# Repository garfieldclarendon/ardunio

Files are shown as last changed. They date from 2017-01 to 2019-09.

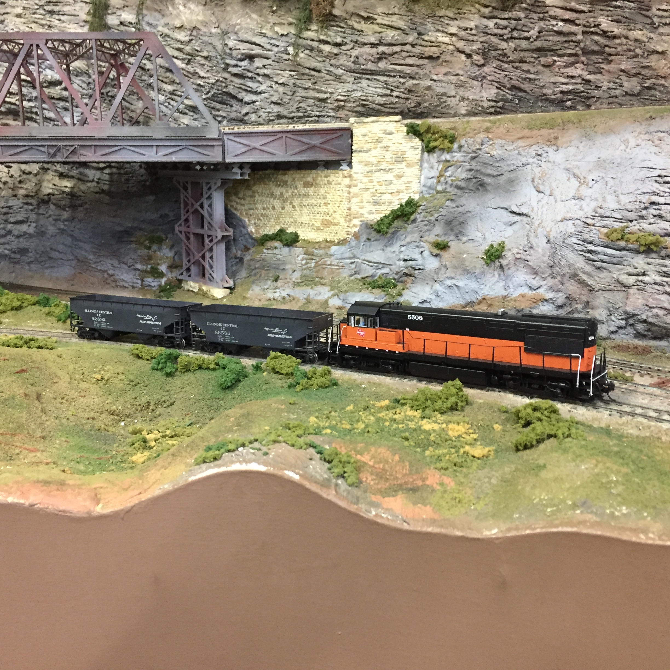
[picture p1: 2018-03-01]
Documents/Images/Train_enroute.JPG

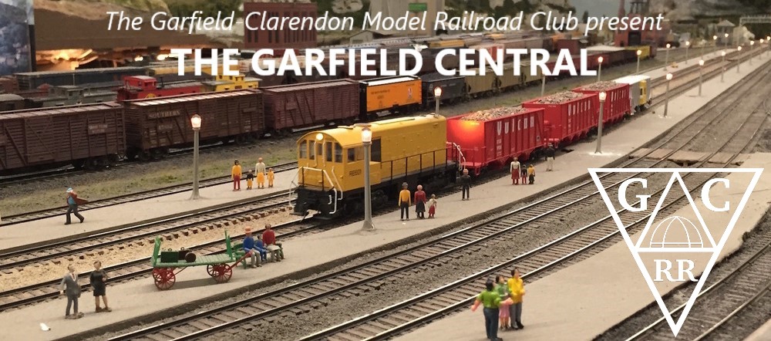
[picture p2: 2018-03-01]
Documents/Images/LayoutPic1.jpg

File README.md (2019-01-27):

# Layout Control System (LCS)

A project that uses ESP8266 WiFi modules that communicate with a Raspberry Pi server to control accessories on the Garfield-Clarendon Model Railroad Club.

### Prerequisites

The code running on the ESP8266 is developed using the Arduino IDE

The LCSServer application running on the Raspberry Pi makes use of the Qt framework.  The ESP8266 uses http calls to communicate with the LCSServer application  and UDP unicast messages to communicate with other ESP8266 controllers on the layout.  A separate RESTful API provides access to commands to activate routes, set turnouts and update data in the configuration database.

[Layout Control System Overview](https://github.com/garfieldclarendon/garfieldclarendon.github.io/blob/master/html/Documents/LCSOverview.pdf)

[Source Code Documentation](https://garfieldclarendon.github.io/html/index.html)

[API Documentation](https://garfieldclarendon.github.io/apidoc/index.html)

## Built With

* [Arduino](https://www.arduino.cc/en/Main/Software) - Arduino Tools
* [Qt](https://www.qt.io/) - Qt Framework
* [Eagle](https://www.autodesk.com/products/eagle/overview) - Eagle Printed Circuit Board (PCB) design software

## Contributing

Please read [CONTRIBUTING.md](https://gist.github.com/PurpleBooth/b24679402957c63ec426) for details on our code of conduct, and the process for submitting pull requests to us.

## Authors

* **John Reilly** - *Initial work*
* **Ryan Balla** - *Web Development*

## License

This project is licensed under the MIT License - see the [LICENSE](LICENSE) file for details

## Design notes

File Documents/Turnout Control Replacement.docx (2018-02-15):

# Turnout Control Replacement

# What You’ll Need

- Turnout motor cable
- Turnout Module (if needed. Each module controls two turnout motors)
- Communication Cable (for new module only)

# Installation

## Converting a turnout to LCS control involves 5 basic steps:

1. Enter the device and route entries into the LCS database.
2. Install the Turnout Module
3. Connect the turnout motor to the Turnout Module
4. Connect the Red and Green LED’s to the control panel(s) Output Module
5. Connect the panel button/switches to the control panel(s) Input Module

## Update the LCS software database:

1. Add the Turnout Device to the LCS System (Screen shot)
2. Identify which Turnout Module the new turnout device is going to be connected to. If this is a new module, add the module to the LCS System (Screen Shot)
a. Edit the new Turnout Device entry.
b. In the Assigned Controller Modules list, add a new entry - selecting the module identified in step 2 above. Enter the port number (0 or 1) to which the turnout will be wired. 0 is the bottom connection, 1 is the top. Each port is labeled on the circuit board.
3. In the search box, enter the name of the turnout created in step 1 above. Three entries should appear; the turnout device entry and two PanelOutput device entries which were automatically created with the turnout device. These entries will have the same name as the turnout with (Red) and (Green) appended to the end of the name.
a. Identify which Output Module the two LED’s are going to be wired to. Do this for each panel the turnout is displayed on.
b. Edit each PanelOutput device entry
c. In the Assigned Controller Modules list, add a new entry - selecting the module identified in 3.a. Enter the pin number the LED will be wired to. Starting at the bottom of the right output connector, the pins are numbered 0 – 7 then continue from the top of the left output connector numbered 8-15.
4. Add the route
a. Add the route entries
5. Add new PanelInput devices for each button/switch. NOTE: Add only one entry even if the button activates the turnout from more than one panel.
a. Identify the Input Module the button/switch will be connected to. Do this for each panel the turnout is controlled from.
b. Edit each PanelInput device entry
c. In the Assigned Controller Modules list, add a new entry - selecting the module identified in 5.a. Enter the pin number the button/switch will be wired to. Starting at the bottom of the right input connector, the pins are numbered 0 – 7 then continue from the top of the left input connector numbered 8-15.
6. Install the Turnout Module (if a new module is required). DO NOT CONNECT THE COMMUNICATION CABLE
7. Connect the turnout cable to the turnout motor and plug the cable into the assigned port.
8. Disconnect power from the controller
9. Verify the address dip-switch settings
10. Connect the communication cable
11. Connect power to the controller.
12. Verify the turnout is set to its normal position.
13. Verify the status of the turnout in the Admin application (screen shot)

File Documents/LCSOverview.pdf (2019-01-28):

## Garfield-Clarendon Model Railroad Club

# Layout Control System

### LCS Overview

The Layout Control System or LCS is a micro-controller based system used to control model railroad accessory devices such as turnout motors, signals, control panels, etc. The system is based around the ESP-12F ESP8266 (https://en.wikipedia.org/wiki/ESP8266) Wi-Fi module. This low cost, Wi-Fi-microcontroller module has the perfect combination of power and features which makes it ideally suited for a project of this type. For the purpose of this overview, the Layout Control System is referred to as “LCS” throughout this document.

4501 N Clarendon Avenue
Chicago, IL 60640

# Layout Control System

LCS Overview

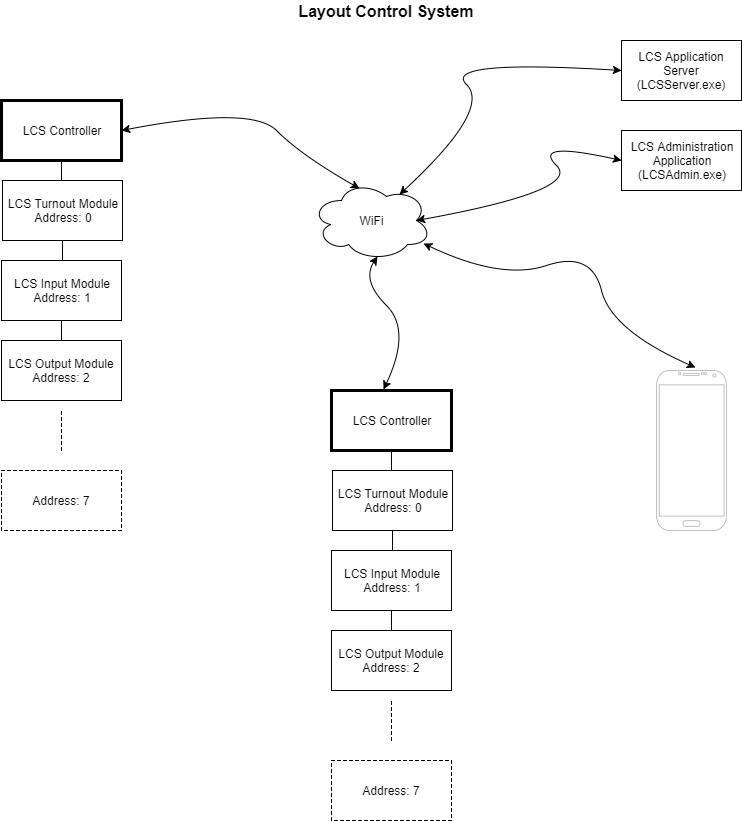
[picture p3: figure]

Figure 1 LCS Overview

# Layout Control System

LCS Overview

As pictured, LCS is broken down into the following components:

Controller | The ESP8266 based micro-controller board that controls the attached accessories. Each controller board can communicate with up to 8 module boards over the I2C (https://en.wikipedia.org/wiki/I%C2%B2C) serial bus.
Turnout Module | Controls two turnout motors and receives feedback from the turnout motor as to its current position (normal or thrown)
Input Module | 16 input pins are available to be used by control panel buttons and/or block detection units
Output Module | 16 output pins are available to be used by control panel LED’s and/or signals
Application Server | The application that manages the database which stores the configuration data that drives the system. The application server also acts as the interface between outside systems such as the NCE Command Station, smart phones, dispatcher panels, etc.
Administration Application | A user-friendly application for managing the system configuration data.

Table 1 LCS Components

### LCS Controller

The controller provides processing and communication. There are three types of controllers:

Class | Controller Type | Description
7 | Multi-Controller | The most common controller type. This controller manages multiple module boards connected via an I2C (https://en.wikipedia.org/wiki/I%C2%B2C) serial bus cable.
1 | Turnout Controller | A controller and turnout module combined into one board which can control two turnouts.
5 | Semaphore Controller | Semaphore Signal Controller which is a controller and turnout module combined into one board. The turnout module is used to run the motor that moves the signal arm.

Table 2 Controller Types

Most of the controllers on the layout will be the Multi-Controller as it can handle many more devices. Since we have only one Semaphore signal on the layout, there’s only one Semaphore Controller. Although there are three controller types,

# Layout Control System

LCS Overview

there are only 2 actual controller printed circuit boards. The Semaphore Controller uses the same board as the Turnout Controller. Internally, the three controllers use the same firmware. The firmware code knows what controller it’s actually running on based on the Controller Class setting in the controller’s configuration file (described shortly).

### LCS Modules

The LCS Controller does not directly control devices. Rather, each controller may have up to 8 module boards connected which, in turn, control the attached devices. There are 4 types of module boards (see Table 5). Module boards are connected using a communication cable (figure 2).

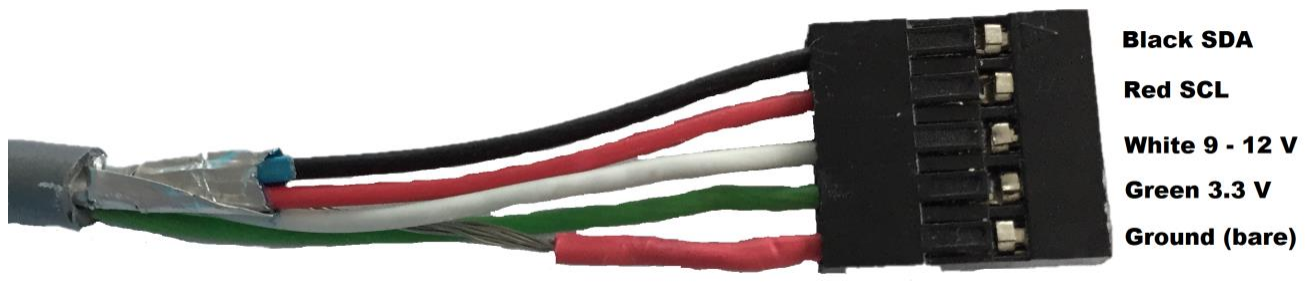
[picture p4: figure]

Figure 2 Communication Cable

The black and red (SDA, SCL) wires are the actual communication wires used by the I2C (https://en.wikipedia.org/wiki/I%C2%B2C) bus. The white wire acts as a pass-through power source which can be used by modules to power devices that require higher voltages (like turnout motors). Although labeled as 9 – 12 V, the voltage is actually the same as the power supply plugged into the controller board. If the power supply is a 9 volt power supply, then the voltage between the white wire and the ground (red) wire will be 9 volts. The green wire is the 3.3 V output of the voltage regulator on the controller board. The regulator will adjust the input voltage to keep it as close to 3.3 volts as possible. This supplies the regulated voltage needed by the IC chips on the module boards.

Each module has a corresponding entry in the database which defines the module’s type, which controller it’s connected to and the module’s address. Module boards must have a unique address of 0 to 7. To achieve this, a three-position dip switch is used to set the module’s address:

# Layout Control System

LCS Overview

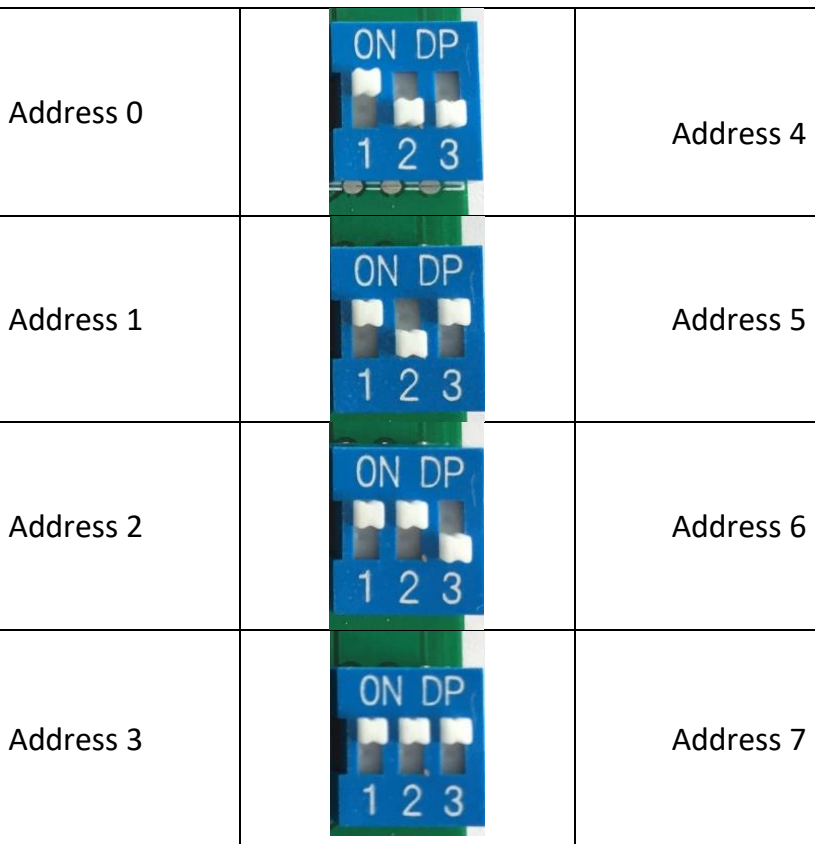
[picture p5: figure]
Address 0; Address 4; Address 1; Address 5; Address 2; Address 6; Address 3; Address 7
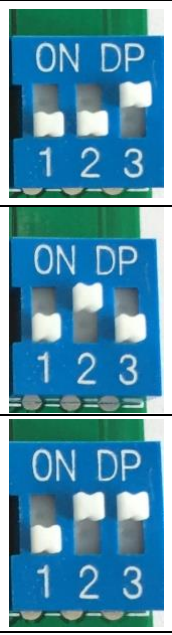
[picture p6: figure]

Table 3 Address DIP switch settings

NOTE: The address set with the dip switches must match the address entered in the module’s entry in the database. Module boards may be connected to the controller in any order.

### LCS Device

LCS treats everything it interacts with as a device. A device represents an item on the layout that the system either controls or monitors. LCS supports the following types of devices:

# Layout Control System

LCS Overview

Turnout | A slow-motion motor Which controls a turnout on the layout.
Panel Input | A momentary push-button or switch on a layout control panel. These buttons, when pressed, activate a route which aligns one or more turnouts to a desired route
Panel Output | A panel LED indicator light. The LED indicates the current state of a turnout , route or block occupancy.
Signal | A three-light (LED) signal head.
Block Occupancy Detector | Monitors an external block detection circuit.

Table 4 Device Types

Like modules, each device has a corresponding database entry which defines the device type, assigned module and the port (pin) on the module the device is connected to.

### LCS Configuration Files

JSON (https://en.wikipedia.org/wiki/JSON) formatted configuration files are stored in the controller’s permanent flash memory. When the controller starts up, the first file it loads is the controller’s configuration file:

{
"controllerClass": "7",
"controllerID": "34",
"controllersToNotify": [{
"controllerID": "28"
}
],
"modules": [{
"address": "0",
"class": "8"
}, {
"address": "1",
"class": "9"
}, {
"address": "2",
"class": "9"
}
]
}

This is the configuration file for the CA Auxiliary control panel. Here’s what the entries mean:

“controllerClass” contains a number that represents the type of controller board (see table 2)

# Layout Control System

LCS Overview

“controllerID” contains the unique ID of the controller from the controller table in the database. Each controller is identified by a controllerID and a serialNumber. The controllerID entry is used to cross-reference the controller with the modules connected to it. The serial number is a unique id assigned by the manufacturer to each ESP8266 Wi-Fi module. The reason for the two identifiers is so that if a controller needs to be replaced, the only field that needs to be updated in the database is the serial number field.

“controllersToNotify” is a list of controller ID’s that need to be notified whenever the state of a connected device changes. Since this configuration is from the CA Auxiliary panel, the device that will trigger a notification message is a Panel Input device (panel button). When the user presses a button on the panel, the Panel Input Device will generate a message which will be sent to each controller listed in this section. In this example just one controller will be notified which is controller 28 – “CA West End Multi 1” controller.

“modules” is a list of modules connected to this controller via the I2C (https://en.wikipedia.org/wiki/I%C2%B2C) serial bus . Each module entry contains the address of the module and the module class:

Class | Module Type | Software Module Class
1 | Turnout Module | TurnoutModule
5 | Semaphore Module | TurnoutModule
8 | Input Module | InputModule
9 | Output Module | OutputModule
Table 5 Module Types

In this example, three modules are connected; an input module (class 8) and two output modules (class 9) with the addresses of 0, 1 and 2 respectively.

Next, the LCS Controller creates software modules that manage the interaction between the physical module board and the devices connected to the module. The LCS Controller communicates with each module via the I2C serial bus communication cable (Figure 2).

Each module’s configuration file is the next file to be loaded:

# Layout Control System

LCS Overview

{
"devices": [{
"c": "2",
"id": "44",
"p": "0"
}, {
"c": "2",
"id": "43",
"p": "1"

}, {
"c": "2",
"id": "52",
"p": "15"
}
],
}
Each JSON file contains a list of devices attached to the controller module. In this example, the devices are all the same; device class 2 – Panel Input, as defined by the “c”: “2” entry. Each device entry in this example file represents a button on the CA Auxiliary Panel. The other two properties in the device configuration represent the device ID “id” and the pin assignment “p”. Putting it all together, the first entry is a Panel Input device (2) with a device ID of 44 (id) and is assigned to pin 0 (p). For each entry in the file, a software class that manages the device is created. This software class has all the logic needed to manage the device. Once an instance of the device class is created, the next step is to load the configuration data for that device. As you probably guessed, this involves loading a JSON file for each device attached to the controller module:

{
"ROUTEID": "19",
"deviceClass": "2"
}

Continuing with the previous example, this is the configuration for the first device entry, device 44. The important line in this file is the ROUTEID entry. This represents the route that gets activated when the button connected to pin 0 is pressed on the CA Auxiliary Panel.

The reality is, the configuration files are not actually stored as JSON files. The reason is these files must be loaded and then parsed by the micro-controller and converted to a binary structure it can actually use. This process is pretty slow, so instead, the binary structure is what is actually stored in the file. The JSON format is only used when the controller needs to download the configuration files from the

# Layout Control System

LCS Overview

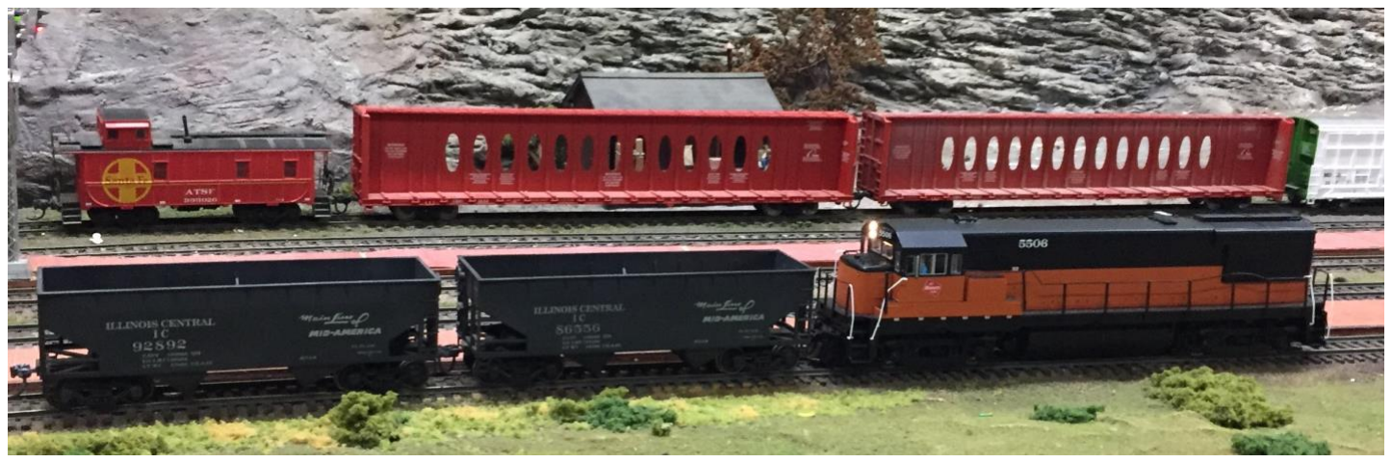
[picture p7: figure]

server. Once downloaded, the JSON information is parsed and converted to the binary structure and saved to a file.

### LCS in Action

The best way to understand how a system works is by following an example. Let’s do a simple run to the Gaskill Mine.

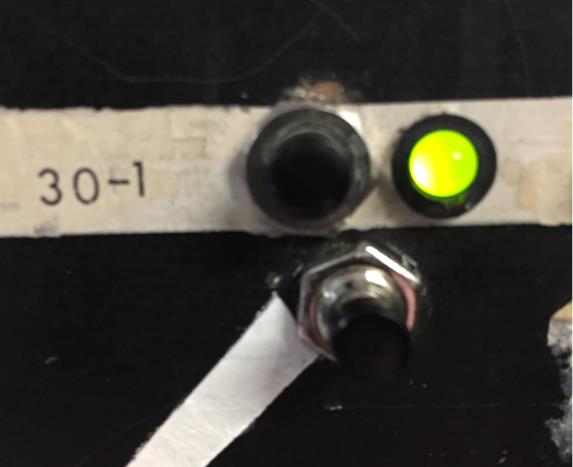
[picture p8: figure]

Milwaukee Road 5506 has two empties to drop off at the Gaskill Mine and awaits the turnout alignment to proceed into the mine branch. Currently, the mine’s turnout, T30-2, is aligned for the main, its normal route, as indicated by the green LED indicator on the CA panel.

In order to route the train to the mine branch, we need to press the bottom button. But what is really happening when the button is pressed?

# Layout Control System

LCS Overview

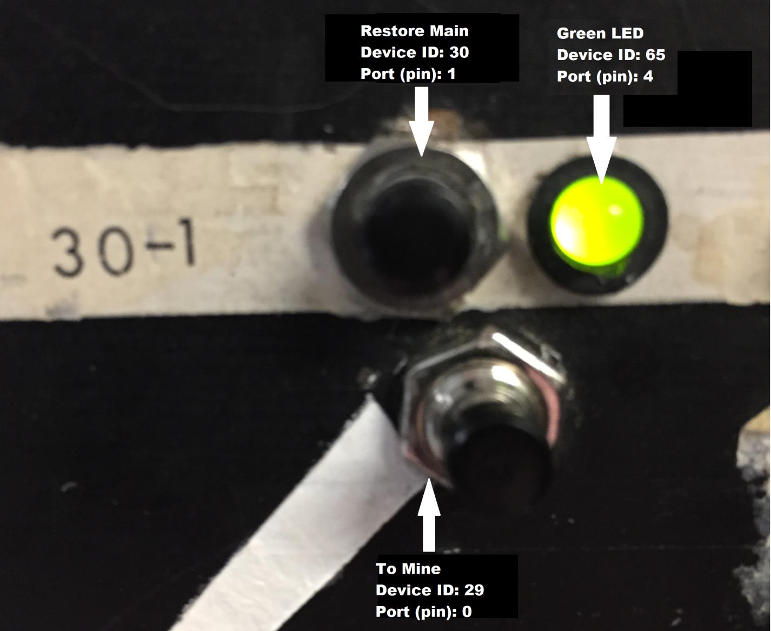
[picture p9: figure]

LCS treats each item it interacts with as a device. In the picture above, we have three devices listed; two buttons and one LED. The reality is, as we’ll see in a moment, there are really 4 devices as the LED is really two LEDs in one package; a red and a green. Notice that each device has a name, a unique ID and a port/pin assignment. In addition each device is assigned to a module that actually controls the device. In this example there are two modules; an Input Module and an Output Module. Let’s look at the database entries that make up this example:

# Layout Control System

LCS Overview

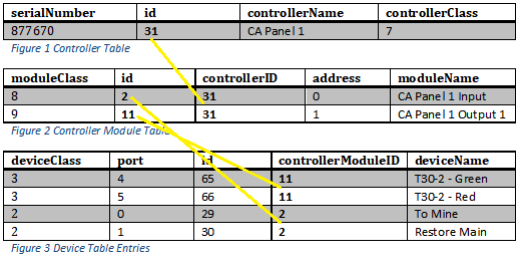
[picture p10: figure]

Note the additional entry in the device table (figure 3) for the “T30-2 – Red” LED device. Also note how the entries in each table are crossed reference with the table above it: The controller entry of id 31 is cross referenced in each entry in the module table via the controllerID field. Each device is cross referenced with its assigned module via the controllerModuleID field. Using this information, the controller has almost everything it needs to manage the buttons and LEDs. It knows how to interact with each device but not when each device LED should be on or off. For that information, we need to dig a little deeper into each device entry.

Devices have properties that are unique to each device type. These properties are stored in another database table called “deviceProperty”. Let’s look at the first button we’re going to press, the “To Mine” button, and examine its device property entry:

id | deviceID | key | value
7 | 29 | ROUTEID | 7
Figure 3 Device Property Table

This type of table is referred to in programming terms as a “key/value pair” table. In this case, “ROUTEID” is the key and “7” is the value. This data is used by the PanelInputDevice class to know what route to activate when a button is pressed; in this case, route 7.

As you probably guessed by now, each route is stored in its own database table called “route” and has a corresponding table, “routeEntry”, which contains an entry

# Layout Control System

LCS Overview

for each turnout the route needs to set when the route is activated. Let’s take a look at route 7:

id | routeName | routeDescription
7 | CA 1 | To Mine
Figure 4 Route Table
id | routeID | deviceID | turnoutState
11 | 7 | 7 | 3
Figure 5 Route Entry Table

Route 7 has one Route Entry item; Turnout device ID 7 (T30-2). When route 7 is activated, the Turnout Device will set the turnout with ID 7 to the turnout state of 3 (Diverging).

Let’s put it all together. When we push the bottom button, the InputModule will detect that the pin that button is connected to, pin 0, has changed. This information is passed on to the PanelInputDevice which activates route 7. How is route 7 actually activated? By sending a message!

UDPMessage and the Wi-Fi Network

The way one controller talks to another controller and the Application Server is via the Wi-Fi network. Because the ESP8266 is a very basic micro-controller with limited speed and memory, we need an efficient, low-overhead solution for sending messages between devices. The User Datagram Protocol, UDP, (https://en.wikipedia.org/wiki/User_Datagram_Protocol) is the ideal solution for this problem. UDP is very fast and efficient. The tradeoff is reliability. UDP by itself is an unreliable protocol, meaning there is no guarantee the message will actually reach its intended destination. The LCS Controller compensates for this by retrying each message until it reaches its target controller.

In our example, the PanelInputDevice creates a UDPMessage (https://garfieldclarendon.github.io/html/class_u_d_p_message.html) containing the route ID of 7 which is sent to the controllers in the Notification List from the controller 31’s configuration file. In this file is the controllersToNotify section:

"controllersToNotify": [ { "controllerID": "28" } ]
In this case, the message is sent to controller “28 - CA West End Multi 1” which is the controller that the T30-2 turnout is connected to.

# Layout Control System

LCS Overview

On the receiving end, controller 28 forwards the message to the TurnoutDevice that is managing T30-2. Let’s take a look at its configuration file:

{
"deviceClass": "1",
"routes": [{
"routeID": "7",
"turnoutState": "3"
}, {
"routeID": "8",
"turnoutState": "1"
}
]
}
As you can see, each turnout stores the routes its’ assigned to and the state they need to be set to when the route is activated. In our example, when the message arrives, TurnoutDevice T30-2 will lookup route 7 and set its state to “3 – Diverging”. It then immediately sends out a new message indicating the turnout is now changing by setting its current state to “2 – To Diverging” indicating the turnout is in the process of throwing to the diverging route. The TurnoutDevice’s status message is sent to controller 28’s notification list:

"controllersToNotify": [{
"controllerID": "31"
}, {
"controllerID": "34"
}, {
"controllerID": "35"
}, {
"controllerID": "30"
}
]
Notice there are many more controllers that need to be notified when something connected to controller 28 changes! The first controller in the list is our example controller,”31 - CA Panel 1”. It also sends messages to:
- 34 - CA Aux Panel
- 35 - Overhead Panel
- 30 - Semaphore1
Controller 31 forwards this message to the PanelOutputDevices that manage device ID “65 – T30-2 Green” and device ID “66 – T30-2 Red”. The device properties for device 65 are:

# Layout Control System

LCS Overview

id | deviceID | key | value
89 | 65 | ITEMID | 7
90 | 65 | ONVALUE | 1
91 | 65 | FLASHINGVALUE | 4

ITEMID is set to the device the PanelOutputDevice is monitoring; in this case device ID “7 – T30-2” and sets its output pin ON when T30-2 is “1 – Normal” and flashing when T30-2 is “4 – To Normal”. In our example, the current state of T30-2 is “2 – To Diverging”. Since this doesn’t match either of the two entries, the PanelOutputDevice sets the output to LOW turning the green LED off.

Device 66 has the following entries:

id | deviceID | key | value
89 | 66 | ITEMID | 7
90 | 66 | ONVALUE | 3
91 | 66 | FLASHINGVALUE | 2

Which means T30-2’s current state of “2 – To Diverging” matches its FLASHINGVALUE entry, so the PanelOutputDevice sets the output to a blinking state; turning the red LED ON and then OFF every ¾ of a second.

The result is T30-2 goes from its normal route:

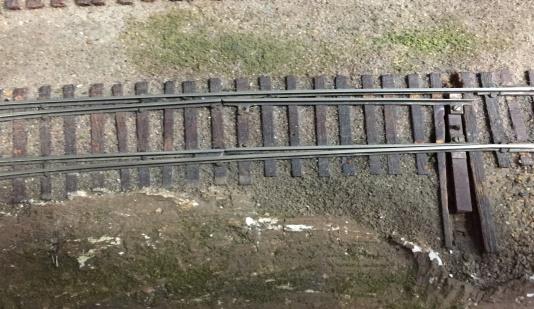
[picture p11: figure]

To its diverging route:

# Layout Control System

LCS Overview

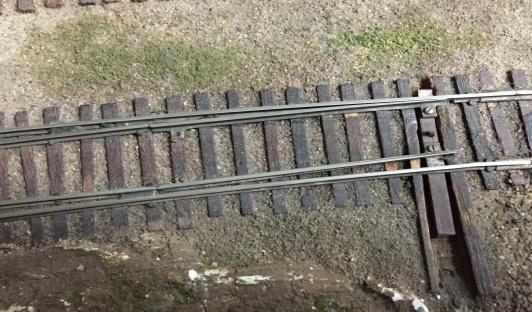
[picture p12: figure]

Now that the turnout is fully thrown, the TurnoutDevice sends a final status message, this time with the status of “3 – Diverging” as T30-2’s current state. The new state of 3 matches the PanelOutputDevice 66’s ONVALUE configuration entry so it sets the output to ON turning on the red LED (the LED stops flashing).

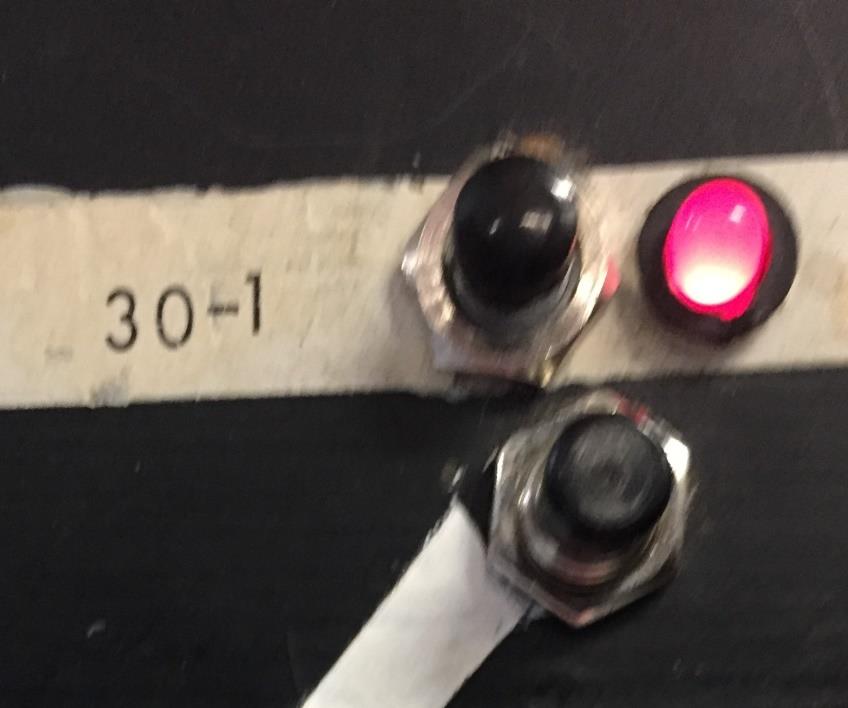
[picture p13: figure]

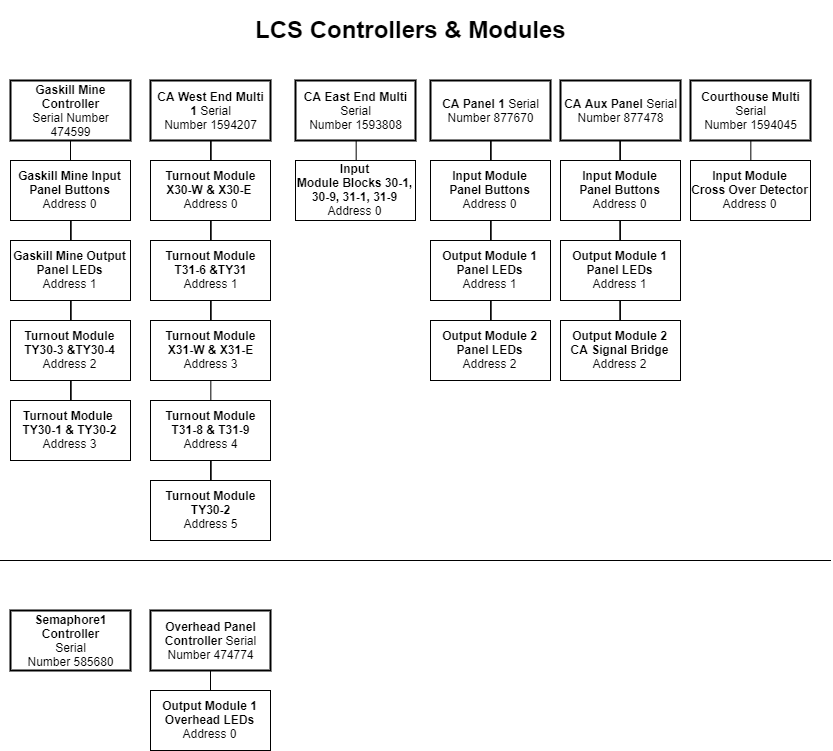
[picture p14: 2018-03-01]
Documents/Images/Overview1.png

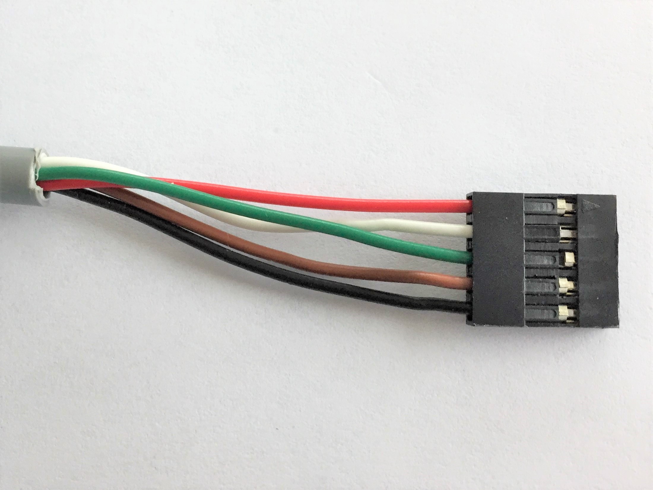
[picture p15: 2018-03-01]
Documents/Images/Turnout_Module_Cable.JPG

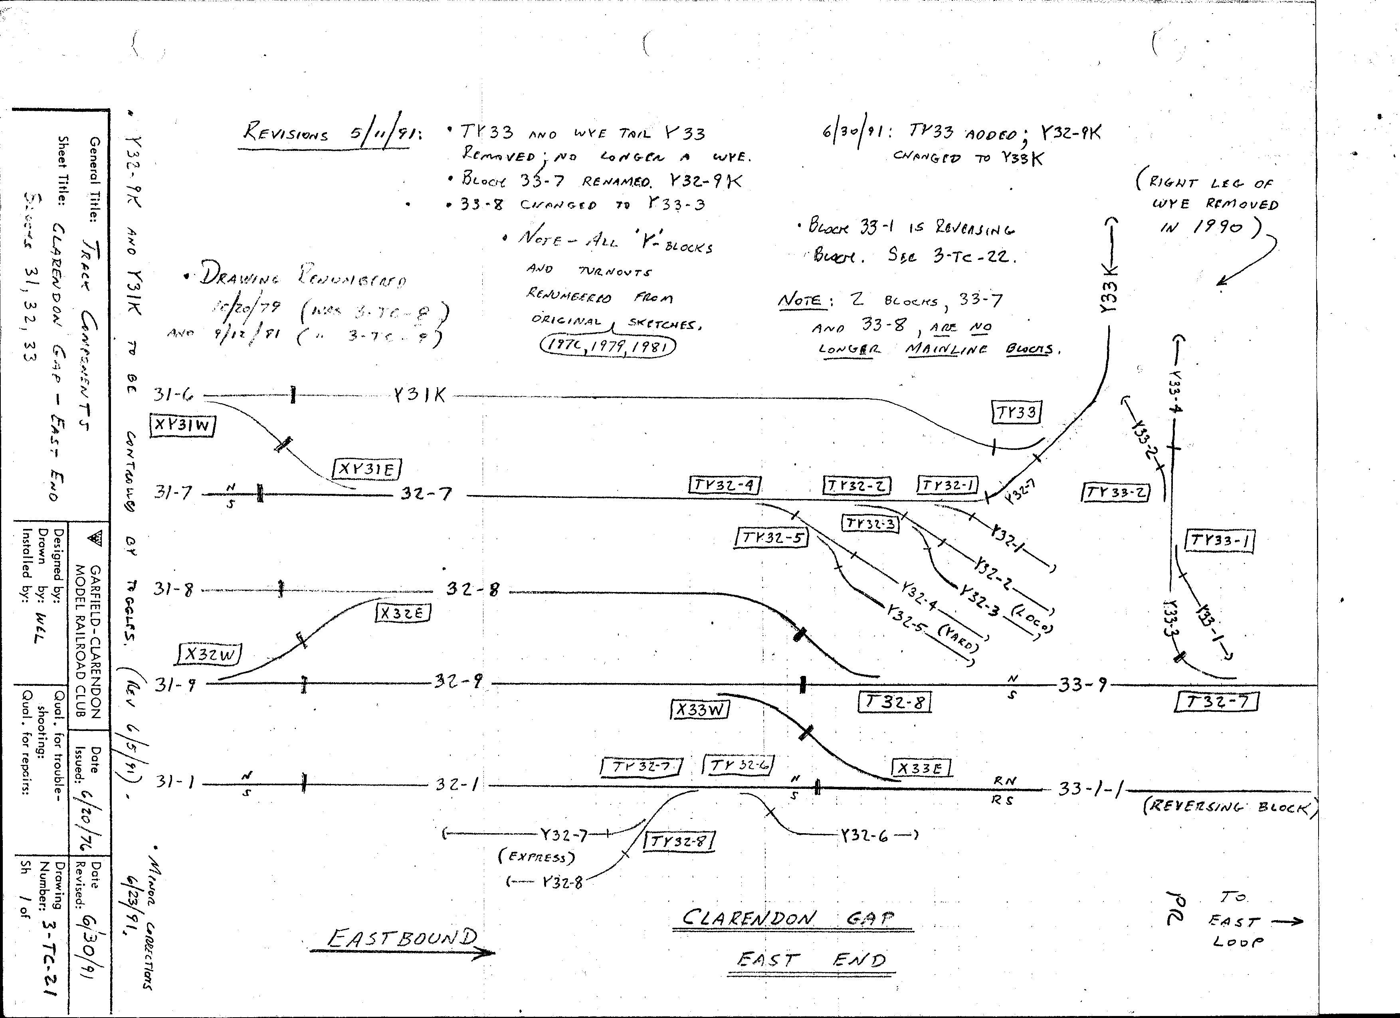
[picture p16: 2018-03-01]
Documents/Images/CA_EastEnd.png

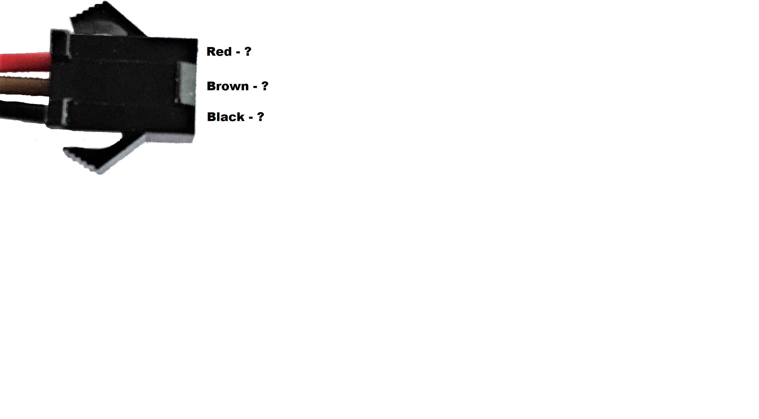
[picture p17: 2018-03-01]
Documents/Images/Turnout_Frog_Cable.png

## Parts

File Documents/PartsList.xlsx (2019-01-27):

MASTER PARTS LIST
ITEM | QUANTITY | COST | PER | STOCK
Resistors - 10k Ohm | 100 | $4.04 | $0.04 | 110
Resistors - 3.3k Ohm | 100 | $6.16 | $0.06 | 119
Resistors - 220 Ohm | 100 | $6.43 | $0.06 | 160+
DIP Switch - 3 position | 20 | $13.64 | $0.68 | 3
Connector - 1x8 Dupont | 10 | $3.30 | $0.33
Connector - 1x5 Dupont | 10 | $3.84 | $0.38
DC Power Jack Socket | 22 | $5.62 | $0.26 | 13
L293D Stepper Motor Driver | 10 | $8.99 | $0.90 | 14
ESP-12F ESP8266 Wifi Controller | 10 | $26.00 | $2.60 | 15
LD1117V33 Voltage Regulator 3.3v | 12 | $7.99 | $0.67 | 6
MCP23017-E I2C Expander (16 pin) | 25 | $26.25 | $1.05 | 8
MCP23008-E I2C Expander (8 pin) | 10 | $10.80 | $1.08 | 13
Single Row 40Pin Male Header | 100 | $8.99 | $0.09
Capacitor 10 uF | 1000 | $13.99 | $0.01 | 900+
Capacitor 1 uF | 100 | $5.63 | $0.06 | 60
LED Red | 100 | $6.57 | $0.07 | 13
Printed Circuit Board | 40 | $43.00 | $1.07
LCS CONTROLLER
Capacitor 10 uF | 1 | $0.01 | $0.01
Capacitor 1 uF | 1 | $0.06 | $0.06
5 Pin Male Header | 9 | $0.01 | $0.10
DC Power Jack Socket | 1 | $0.26 | $0.26
Resistors - 220 Ohm | 2 | $0.06 | $0.13
Resistors - 3.3k Ohm | 2 | $0.06 | $0.12
ESP-12F ESP8266 Wifi Controller | 1 | $2.60 | $2.60
LD1117V33 Voltage Regulator 3.3v | 1 | $0.67 | $0.67
LED Red | 1 | $0.07 | $0.07
Printed Circuit Board | 1 | $1.07 | $1.07
 |  |  | ------------
TOTAL |  |  | $5.09
LCS INPUT MODULE
Capacitor 10 uF | 1 | $0.01 | $0.01
5 Pin Male Header | 2 | $0.01 | $0.02
8 Pin Male Header | 2 | $0.02 | $0.04
MCP23017-E I2C Expander (16 pin) | 1 | $1.05 | $1.05
Resistors - 10k Ohm | 3 | $0.04 | $0.12
Resistors - 3.3k Ohm | 16 | $0.06 | $0.99
DIP Switch - 3 position | 1 | $0.68 | $0.68
Printed Circuit Board | 1 | $1.07 | $1.07
 |  |  | ------------
TOTAL |  |  | $3.99
LCS OUTPUT MODULE
Capacitor 10 uF | 1 | $0.01 | $0.01
5 Pin Male Header | 2 | $0.01 | $0.02
8 Pin Male Header | 2 | $0.02 | $0.04
MCP23017-E I2C Expander (16 pin) | 1 | $1.05 | $1.05
Resistors - 10k Ohm | 3 | $0.04 | $0.12
Resistors - 220 Ohm | 16 | $0.06 | $1.03
Printed Circuit Board | 1 | $1.07 | $1.07
DIP Switch - 3 position | 1 | $0.68 | $0.68
 |  |  | ------------
TOTAL |  |  | $4.03
LCS TURNOUT MODULE
Capacitor 10 uF | 1 | $0.01 | $0.01
5 Pin Male Header | 4 | $0.13 | $0.53
L293D Stepper Motor Driver | 1 | $0.90 | $0.90
Resistors - 10k Ohm | 3 | $0.04 | $0.12
Resistors - 3.3k Ohm | 4 | $0.06 | $0.25
MCP23008-E I2C Expander (8 pin) | 1 | $1.08 | $1.08
DIP Switch - 3 position | 1 | $0.68 | $0.68
Printed Circuit Board | 1 | $1.07 | $1.07
 |  |  | ------------
TOTAL |  |  | $4.64

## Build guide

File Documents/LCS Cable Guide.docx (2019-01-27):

LCS Cable Guide

Communication Cable

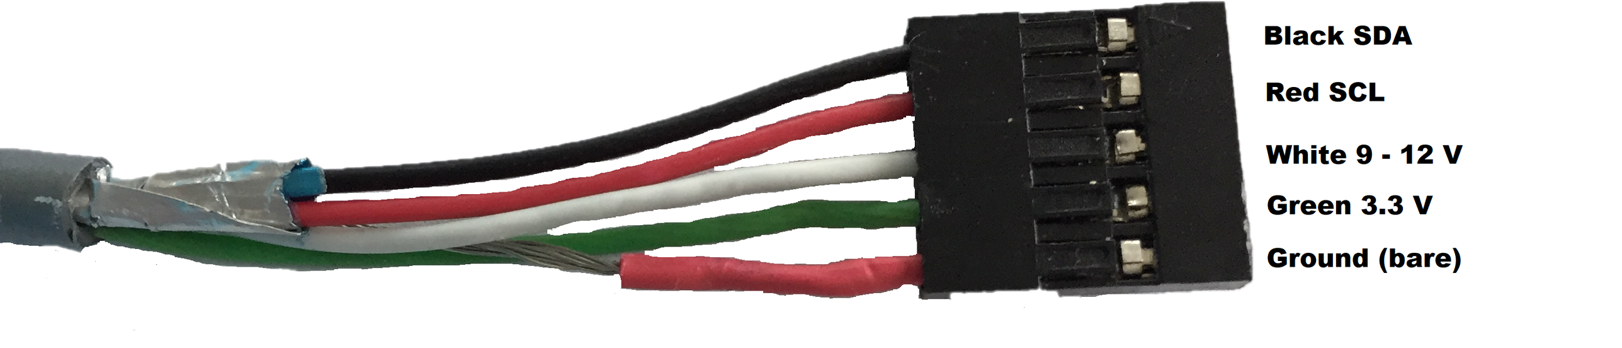
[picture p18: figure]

This cable is used to connect the controller board to module boards. The cable can also be connected between two module boards.

Turnout Motor Cable

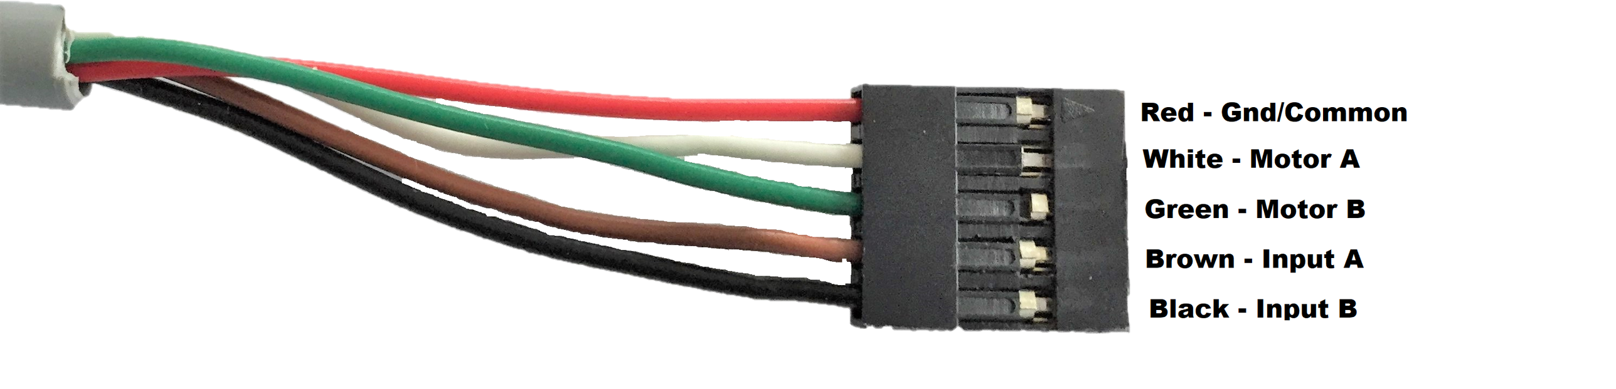
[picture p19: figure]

This cable connects a Turnout Module board to a turnout motor.

Note:

White: Motor +

Green: Motor –

Brown: Signal-Main

Black: Signal Diverging

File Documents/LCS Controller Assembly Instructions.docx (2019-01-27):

Garfield-Clarendon Model Railroad Club

Layout Control System

4501 N Clarendon Avenue

Chicago, IL 60640

LCS Controller Assembly Instructions

# What you’ll need

To assemble a LCS Controller, have the following tools at your side.

1. LCS Controller printed circuit board
2. Soldering iron
3. Solder (Rosin Core)
4. Wire cutters
5. Small screw driver
6. LCS Parts kit

# Getting Started

Plug in your soldering iron and place the LCS Controller circuit board in front of you as pictured

 [picture of blank board]

# Begin Assembly

To make assembly as simple as possible, start by placing the flattest items first followed by taller items in order of height.

1. Begin by soldering the 4 resistors in place. Resistors are labeled as 220 ohm (2) and 3.3 k ohm (2) on the printed circuit board. The orientation of the resistor is not important. [picture with resistors]
2. Place the voltage regulator in place as pictured. [picture with regulator]
3. Bend the voltage regulator backwards until the hole in the regulator’s heat sink aligns with the hole in the circuit board. The hole alignment does not have to be exact. [picture with regulator in place]
4. Solder the voltage regulator in place.
5. Place the pin headers onto the ESP 8266 module. The pin headers can be broken at any pin to create a header with the correct number of pins. Start by lining up the first pin of the header with the first hole in the ESP 8266. With your fingers, mark the last pin. Break the pin header at this point. Do this for both sides of the ESP 8266 module. The pins fit very tightly into the module so it takes a bit of force to properly insert the pins into the unit. It’s easier to place the unit on a flat surface with the pins facing down and firmly press on the center of the ESP9 8266 module until the pins slide into place. Adjusting pressure side-to-side may be necessary to get the pins properly seeded.
6. Very carefully, solder each pin to the ESP 8266. This is, by far, the most challenging soldering job. Be very careful not to let the solder cross over to the adjacent pins or the metal cover.
7. Place the ESP 8266 on the circuit board as pictured and solder into place. [picture with esp8266]
8. Solder the 8 5-pin headers and the 1 4-pin header in place. Like the header for the ESP 8266, these headers are also break-away. [picture with annotations]
9. Solder the 10uf capacitor in place. Align the capacitor with the negative lead (short lead marked with a silver line with a – sign) with the hole marked with a “-“. [picture with 10uf capacitor in place]
10. Solder the .1uf capacitor in place. Align the capacitor with the negative lead (short lead marked with a silver line with a – sign) with the hole marked with a “-“. [picture with .1uf capacitor in place]
11. Solder the red LED in place with the flat side/shorter lead aligned with the bottom hole.
12. Solder the power jack in place as pictured. Use a generous amount of solder on each of the three connections; making sure the solder completely covers the hole.

# Upload Firmware

The unit is now ready to be programmed! To upload the firmware, the LCS Controller needs to be connected to the club’s computer located in the overlook.

1. Plug the programming serial cable into a USB port on the computer and set the switch on the box to “upload”. [picture of the serial cable and box]
2. Connect the other end of the serial cable to the 5-pin header to the left of the ESP 8266 module on the printed circuit board with the blue wire side of the connector aligned with the bottom pin of the header as pictured [cable attached to board with annotation of blue wire]
3. Connect the power supply (from the LCS parts kit) to the LCS Controller. The red LED should light on the controller.
4. Launch the Arduino IDE program by double-clicking the icon on the computer’s desktop [screenshot of desktop]
5. Load the LCSController project. Go to File->Open and browse to the Document->Arduino->LCSController directory. Select the LCSController.ino file:

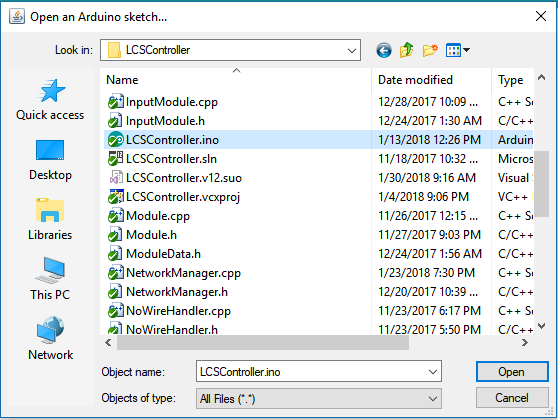
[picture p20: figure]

6. Double check the settings by selecting the Tools menu item. Verify the settings look like this:

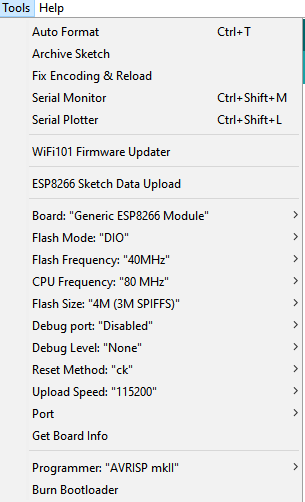
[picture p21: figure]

The important settings are:

- Board: “Generic ESP8266 Module”
- Flash Mode: “DIO”
- Flash Frequency: “40MHz”
- CPU Frequency: “80 MHz”
- Flash Size: “4M (3M SPIFFS)”
- Upload Speed: “115200”
7. Upload the firmware by selecting Sketch->Upload. The Arduino IDE program will compile the LCS Controller firmware and then begin the process of uploading the firmware to the controller. You’ll know the process is working when you see the blue LED on the LCS Controller flashing.
8. After the blue LED stops flashing and the Arduino program indicates the firmware uploaded successfully, unplug the controller.
9. Set the switch on the USB serial cable box to “serial”.???????
10. From the Arduino IDE program, select Tools->Serial Monitor
11. Change the baud rate to 38400 using the drop-down box in the lower right corner. The serial monitor window should look like this: [screen shot of serial monitor]
12. Plug in the LCS Controller.
13. Make note of the serial number printed out in the serial monitor. The LCS Controller will “boot-up” and print out some information about the firmware version number and the controller’s serial number (among other things). Write the serial number on a piece of masking tape and place it on the bottom of the LCS Controller board.
14. Un-plug the unit.

Layout Control System LCS Controller Assembly Instructions

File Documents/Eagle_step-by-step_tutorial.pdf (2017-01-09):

# EAGLE Tutorial

## Introduction

Eagle is a PCB CAD program for designing and laying out printed circuit board (PCB) designs. A freeware version is available as a download, which is what we will use in this Step-by-step tutorial.

http://www.cadsoftusa.com/download-eagle/

EAGLE works in two stages: Schematic capture and PCB design. In the first, the circuit connectivity is designed using the standard component symbols with which we are all familiar. In the second stage, the components are positioned on the printed circuit board and then traces between connected components are laid out. EAGLE makes this easier by preserving the connections between components and also applying various electrical and design rule checks in order to make sure the board will function as expected!

In this tutorial we are going to begin by designing a PCB board for the active low pass filter below, and then in groups of two you will design a PCB for the potentiostat circuit provided in this document. The
low pass filter will have the following component values, and will run off of a | supply.
This gives an approximate cut-off frequency | of 7.95 Hz and a passband gain of -10.

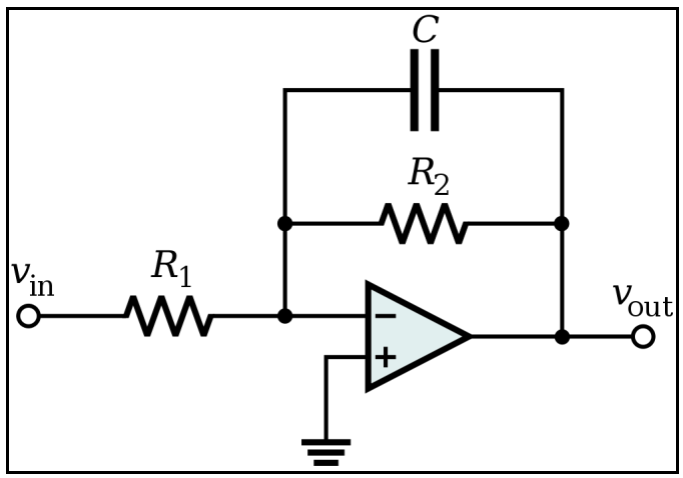
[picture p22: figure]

Figure 1: Active Low Pass Filter Circuit (http://en.wikipedia.org/wiki/Low_pass_filter)

## Part 1: Low Pass Filter

### Getting Started

1. Start Cadsoft EAGLE from the windows start menu (Start → Programs → EAGLE Layout Editor 5.x.x → EAGLE 5.x.x)
2. The first time that you run EAGLE, it will ask whether you would like to create a directory, click yes.
3. Expand the ‘Projects’ node of the tree on the left of the EAGLE menu.
4. Right click on the ‘eagle’ folder and select ‘New Project’. Name it ‘LPF’ (for low pass filter).
5. Right click on the LPF project folder (coloured in red) and select New → Schematic.

### Creating the Schematic

1. Select File → Save and save the schematic as ‘LPF Schematic.sch’.
2. First of all, add all of the parts we will need, in this case that is two resistors, a capacitor, and an opamp. We are going to use 0603 sized resistors and capacitors, and a through-hold DIP (Dual Inline Package) opamp.
a. Click on the ‘Add’ icon on the left-side toolbox – .
b. Start by adding the opamp, type ‘*LM*741*’ into the search box and press Enter.
c. Select the ‘DIL08’ version of the component and click ‘OK’. Click on the schematic to place the part. Press the right mouse button twice to rotate the part and then click the center mouse button once to mirror the part. This will orient the positive and negative terminals of the gate properly.
d. Press ESC to return to the ADD dialog.
e. In the ADD dialog, change the search term to be blank and press Enter.
f. Scroll down until ‘rcl’ appears in the list of parts. Expand ‘rcl’ and then expand the ‘R-US_’. Scroll down to ‘R-US_R0603’, select it, and
press ‘OK’. Place to resistors
g. Press ESC again to return to the ADD dialog.
h. Go back up to the root of the ‘rcl’ library and expand the ‘C-EU’ node.
i. Find the ‘C-EUC0603’ part and press OK. Place the part as per the schematic.
j. Press ESC and then ESC again to exit ADD mode.
3. At this point the schematic should look like Figure 2.
4. Now for the connectivity! Select the ‘NET’ tool from the

toolbox – .

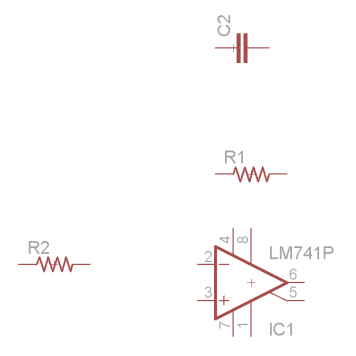
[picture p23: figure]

Figure 2: Basic part pl acement.

5. Draw wires between all of the relevant terminals as per the original schematic. Note: Double click to terminate the current NET. Select the ‘Junction’ tool ( ) and click to place junctions between wires(Automatic Junctions will appear on NETs that overlap).
6. Now we need to add the power and data ports:
a. In the ADD dialog again, place supply2 → GND for the positive pin and also in an open area to connect to the power
supply.
b. Place supply2 → +15Vand
supply2 → -15V both onto the op-amp and also near the
previously placed ground.
c. Finally, we will add input/output plugs for the various signals needed by the board (+15V, ground, -15V, signal input, and signal output).
d. Place a con-lstb → MA05-1 on the schematic near the three floating power symbols.
7. Complete the wiring as per Figure 3.

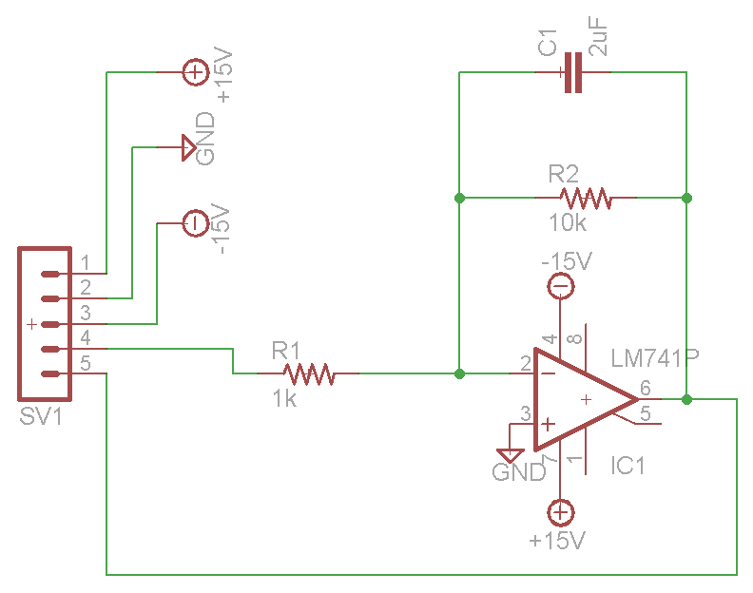
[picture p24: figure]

8. Finally, we will assign component values. Click on the ‘Value’ icon – .
9. Click on each of the resistors R1 and R2, and the capacitor C1 and assign them the values of ‘1k’, ‘10k’, and ‘2uF’ respectively.
10. It is a good idea to run an electrical rules check (ERC) to make sure you haven’t made any mistakes! Click the ‘Electrical Rule Check’ button ( ) and make sure there are no errors or warnings that you are not expecting.
11. Make sure to save the schematic, and then choose File → Switch to board to begin creating the associated PCB.

### Creating the PCB

1. When asked if you would like to create the ‘LPF Schematic.brd’ file, click ‘Yes’.
2. You will now see a blank PCB board, along with the parts from your schematic in the lower left.
a. The parts don’t look the same! These are the footprints associated with the components from the schematic. A footprint is the physical set of pin holes and copper areas that components of a particular side need to be soldered/clipped/connected to.
3. We will begin by positioning the footprints on the board through a combination of rotation and movement. Mirroring a footprint is NOT allowed unless you are putting it on the opposite side of the board. There are more guidelines below (in the ‘tips’ section) but the important factors to consider here are:
a. Make the design compact.
b. Keep in mind that parts exist in 3 dimensions, and just because the footprints fit near each other, does not mean the parts will.

Figure 3: Complete wired schematic.

c. Lay the design out logically to minimize errors now and later on.
d. Try to minimize the number of times that the dark yellow ‘connection guidelines’ cross. Crossing traces means putting vias through the board which is expensive and takes up space.
4. Component footprints can be positioned using ‘Move’ ( | ) and ‘Rotate’ ( ).
5. Using the ‘Delete’ command ( | ), delete the existing board outline. Once the traces are laid
down a new outline can be created to minimize the necessary surface area of the board. PCBs are priced proportionally to the number of holes in them and
their total surface area, so saving space saves money!
6. With your layout completed (Figure 4), it is time to add the
traces. Select the ‘Route’ tool – .
7. Make sure you are working on the side of the board you want. Layers (top or bottom normally) can be selected in the
layer dropdown: | .
8. To add traces to the board, first click on a connected pad, then click to lay the trace and finally click on the ending pad indicated by the dark yellow line. Remember:
a. Keep the traces as short as possible! Longer traces add resistance, thermal noise, and can also act as
antennae.
b. Avoid 90 degree corners, 45 degrees is preferred

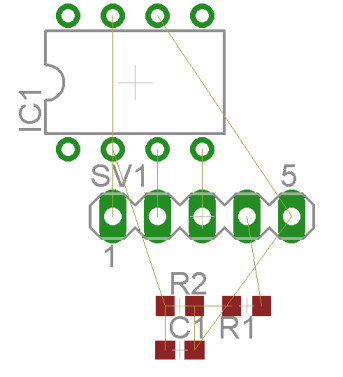
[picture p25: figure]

c. Avoid running two traces in parallel on top of each other on opposite sides of the board. This can cause capacitive coupling between the traces.
d. Make sure traces are wide enough, especially power traces.
9. In order to actually know what goes where after the board is manufactured, it is important to make sure that the component labels (e.g. R1, C1, IC1, etc.) are visible on the silkscreen and won’t be on top of pads or drill holes or anything like that. In order to move the label of a part around, you have to first ‘Smash’ the part ( ) and then select and ‘Move’ the label ( ).
10. The final step is to arrive at the final board outline, which in this case will be a simple square. Select the ‘Line’ tool ( ) and make sure to select the ‘Dimension’ layer. Finally, draw the outline of the PCB board. Make sure to leave a bit of space around the edge of the board.
11. Use the ‘Design Rules Check’ ( ) to ensure there are no overlapping traces or other mechanical problems.

Figure 4: Component
positioning.

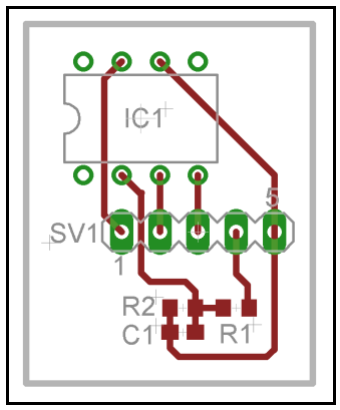
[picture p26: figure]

Figure 5: Final board design

## Appendix: PCB Design Tips

### Component Layout

- Try to lay out the components in a logical way, grouping components and sometimes making the PCB topography reflect the topography of the schematic
- Try to minimize the total surface area required
- Try to minimize the number of crosses in the ratsnest (dark-yellow lines indicating unrouted connections)
- Make sure that not only do the footprints fit around each other, but the 3D structures of the components will not intersect.
- DO NOT mirror a component unless you are putting it on the other side of the board.

### Trace Routing

- Try to minimize trace lengths. Long traces add more resistive losses, more thermal noise, and can act as an antenna.
- Do not run two parallel traces on opposing sides of the board on top of each other, they can become capacitive coupled.
- Avoid 90° angles and T-intersection. Instead always go around corners and merge traces at 45 degree angles
- Ensure that traces are wide enough to carry their current. Trace width calculators are widely available on the internet. This is especially important for power traces.
- Make sure traces are sufficiently spaced, generally at least one trace-width apart.
- Try to ‘balance’ traces on differential-type devices as much as possible.
- If you have room on your circuit, use a ground plane for the ground instead of a trace.

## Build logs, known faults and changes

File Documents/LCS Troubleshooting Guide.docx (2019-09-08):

Garfield-Clarendon Model Railroad Club

Layout Control System

4501 N Clarendon Avenue

Chicago, IL 60640

Troubleshooting Guide

# Overview

When the system is not working correctly, it is usually related to the communication between the LCS Controllers via the club’s Wi-Fi. The issue is usually one of the following:

1. One or more of the LCS controllers are no longer connected to the Wi-Fi.
2. One or more of the LCS controllers are no longer communicating with the module boards connected to it (the I2C serial bus is down)
3. The club’s Wi-Fi network is malfunctioning.

This guide is broken down into Symptoms and Solutions.

# Symptom: A control panel has stopped responding. When a button or switch is pressed, nothing happens.

#### Solution 1: Reset the panel’s controller(s).

1. Find the controller(s) connected to the panel. The controller should be either inside the panel or mounted nearby. The controller has a red power LED.
2. Un-plug the power cable from the controller. Wait a few seconds and plug the power back in.
3. Wait for the board to reboot. This can take up to a minute.
4. If the blue “Wi-Fi connected” LED does not turn on, there is an issue with the club’s Wi-Fi network. See Resetting the Wi-Fi.

# Symptom: A control panel has stopped responding. When a button or switch is pressed, LED’s begin flashing but the turnouts do not throw.

#### Solution 1: The controllers running the turnouts have stopped responding. Reset those controllers

1. Find the controller(s) running the turnouts that are controlled from the panel. Currently, these controllers are located under the east end of CA, behind the main CA panel on the lower right corner and under the west end of CA. The controllers have a red power LED.
2. Un-plug the power cable from each controller. Wait a few seconds and plug the power back in.
3. Wait for the board to reboot. This can take up to a minute.
4. If the blue “Wi-Fi connected” LED does not turn on, there is an issue with the club’s Wi-Fi network. See Resetting the Wi-Fi.

# Symptom: The signals coming into CA stopped working.

#### Solution 1: The controller running the signals has stopped responding. Reset that controller.

1. The signals coming into CA are managed by a controller mounted under the layout near the signals. The controller has a red power LED.
2. Un-plug the power cable from the controller. Wait a few seconds and plug the power back in.
3. Wait for the board to reboot. This can take up to a minute.
4. If the blue “Wi-Fi connected” LED does not turn on, there is an issue with the club’s Wi-Fi network. See Resetting the Wi-Fi.

#### Solution 2: The controllers running the turnouts or the controllers monitoring the block detectors has stopped responding. Reset those controllers.

1. Currently, these controllers are located under the east end of CA, behind the main CA panel on the lower right corner and under the west end of CA. The signals coming into CA are managed by a controller mounted under the layout near the signals. The controller monitoring the block detectors in Bridgeport are mounted in the far right panel in Bridgeport. The controllers have a red power LED.
2. Un-plug the power cable from the controller. Wait a few seconds and plug the power back in.
3. Wait for the board to reboot. This can take up to a minute.
4. If the blue “Wi-Fi connected” LED does not turn on, there is an issue with the club’s Wi-Fi network. See Resetting the Wi-Fi.

# Symptom: The crossing switch indicator on the signal mast and/or on the CA panel is not operating properly.

#### Solution 1: The controller running the crossing switch monitor has stopped responding. Reset that controller.

1. The controller is located in Courthouse mounted under the layout mounted on the same board as the relays controlled by the crossing switch. The controller has a red power LED.
2. Un-plug the power cable from the controller. Wait a few seconds and plug the power back in.
3. Wait for the board to reboot. This can take up to a minute.
4. If the blue “Wi-Fi connected” LED does not turn on, there is an issue with the club’s Wi-Fi network. See Resetting the Wi-Fi.

# Resetting the Wi-Fi

The club’s Wi-Fi system is known as a “Mesh Network” and has multiple Linksys Velop Wi-Fi units:

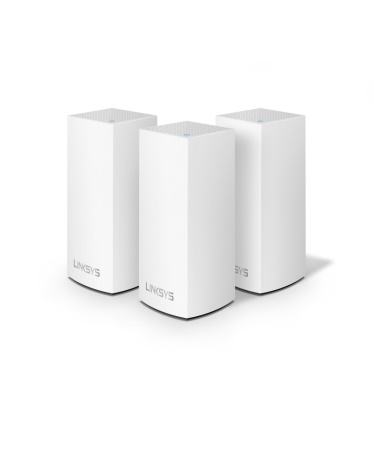
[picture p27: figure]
Linksys Velop Intelligent Mesh WiFi System, 3-Pack White (AC3900) -$ HeroImage

The club currently owns two of these units: one sitting on the large box mounted on the wall behind the overlook and one sitting on the steel bracket next to the center column in the middle of Georgetown. To reset the club’s Wi-Fi, both of these units must be reset.

1. Unplug the unit
2. Wait 30 seconds and plug the unit back in

It takes the Wi-Fi units between 3 – 5 minutes to startup.

BE SURE TO RESTART BOTH UNITS.

Note: Turning the layout off does not turn off the Wi-Fi units. They must be restarted manually.

# Full Restart

If all else fails, restart the entire system and layout.

1. Restart the Wi-Fi network. See Resetting the Wi-Fi.
2. Wait 3 to 5 minutes to give the Wi-Fi a chance to startup.
3. Turn OFF the switch mounted on the wall near the main club entrance.
4. Turn the layout OFF.
5. Wait 30 seconds or so.
6. Turn the layout back ON.
7. Turn ON the switch mounted on the wall near the main club entrance.

January 28, 2019 Version 1.1Page 1

Layout Control System Troubleshooting Guide

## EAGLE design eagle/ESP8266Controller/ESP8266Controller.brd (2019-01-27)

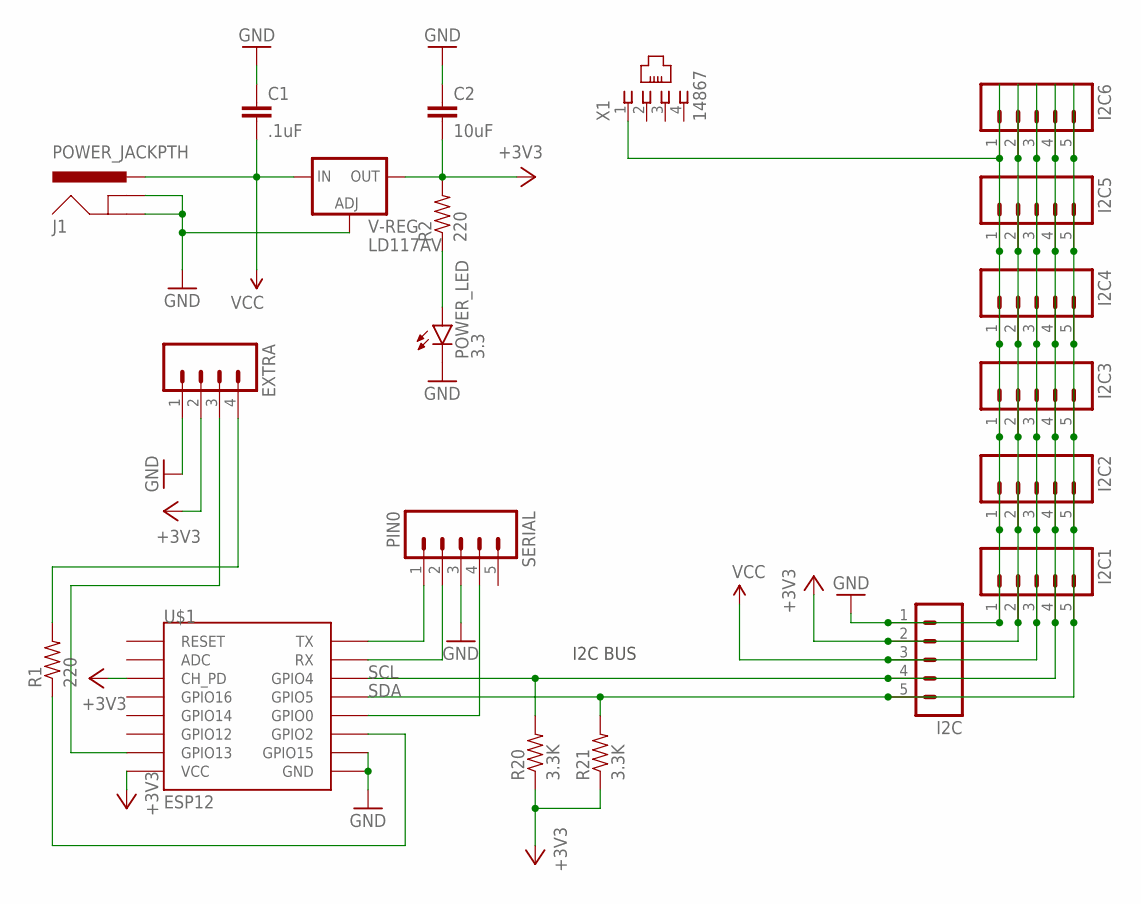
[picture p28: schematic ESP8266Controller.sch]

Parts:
C1: .1uF; CAP-PTH-SMALL
C2: 10uF; CAP-PTH-SMALL
EXTRA: M04; 04P
I2C, I2C1, I2C2, I2C3, I2C4, I2C5, I2C6: M05; 05P
J1: POWER_JACKPTH; POWER_JACK_PTH
POWER_LED: 3.3; LED5MM
R1, R2: 220; AXIAL-0.4
R20, R21: 3.3K; AXIAL-0.4
SERIAL: PIN0; 05P
U$1: ESP12
V-REG: LD117AV; TO220L1
X1: 14867

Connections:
+3V3: C2.2, EXTRA.2, I2C.2, I2C1.2, I2C2.2, I2C3.2, I2C4.2, I2C5.2, I2C6.2, R2.P$2 (2), R20.P$1 (1), R21.P$1 (1), U$1.CH_PD, U$1.VCC, V-REG.2 (OUT)
GND: C1.1, C2.1, EXTRA.1, I2C.1, I2C1.1, I2C2.1, I2C3.1, I2C4.1, I2C5.1, I2C6.1, J1.GND, J1.GNDBREAK, POWER_LED.K (C), SERIAL.3, U$1.GND, U$1.GPIO15, V-REG.1 (ADJ), X1.1
unnamed: EXTRA.4, R1.P$2 (2)
unnamed: R1.P$1 (1), U$1.GPIO2
unnamed: EXTRA.3, U$1.GPIO13
unnamed: SERIAL.1, U$1.TX
unnamed: POWER_LED.A, R2.P$1 (1)
unnamed: SERIAL.2, U$1.RX
unnamed: SERIAL.4, U$1.GPIO0
SCL: I2C.4, I2C1.4, I2C2.4, I2C3.4, I2C4.4, I2C5.4, I2C6.4, R20.P$2 (2), U$1.GPIO4
SDA: I2C.5, I2C1.5, I2C2.5, I2C3.5, I2C4.5, I2C5.5, I2C6.5, R21.P$2 (2), U$1.GPIO5
VCC: C1.2, I2C.3, I2C1.3, I2C2.3, I2C3.3, I2C4.3, I2C5.3, I2C6.3, J1.PWR, V-REG.3 (IN)

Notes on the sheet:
I2C BUS

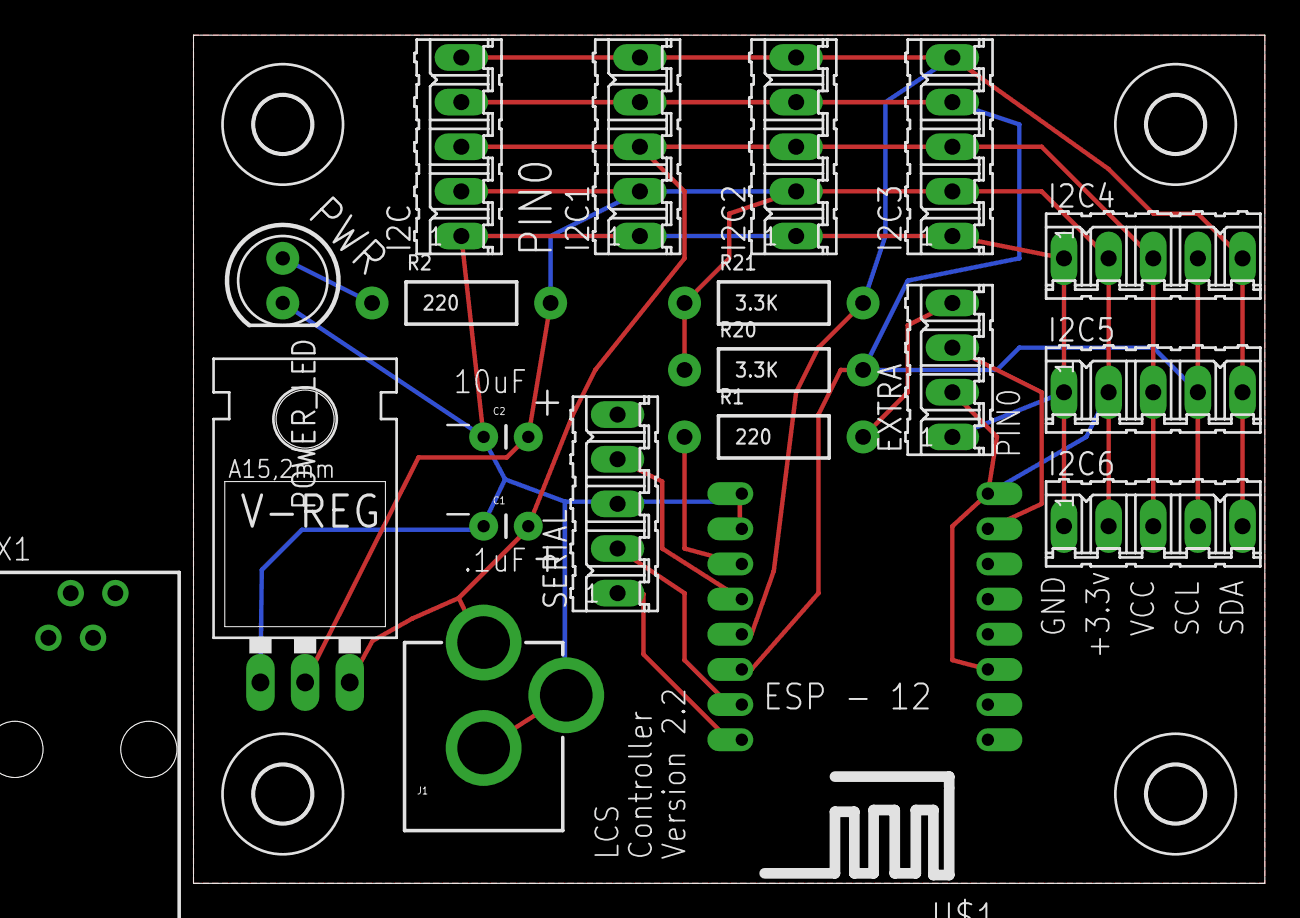
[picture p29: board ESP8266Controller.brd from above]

Board: 2 copper layers, 61.0 x 48.3 mm, 24 parts (0 on the bottom side), 12 nets.

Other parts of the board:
U$2, U$3, U$4, U$5: 3,2

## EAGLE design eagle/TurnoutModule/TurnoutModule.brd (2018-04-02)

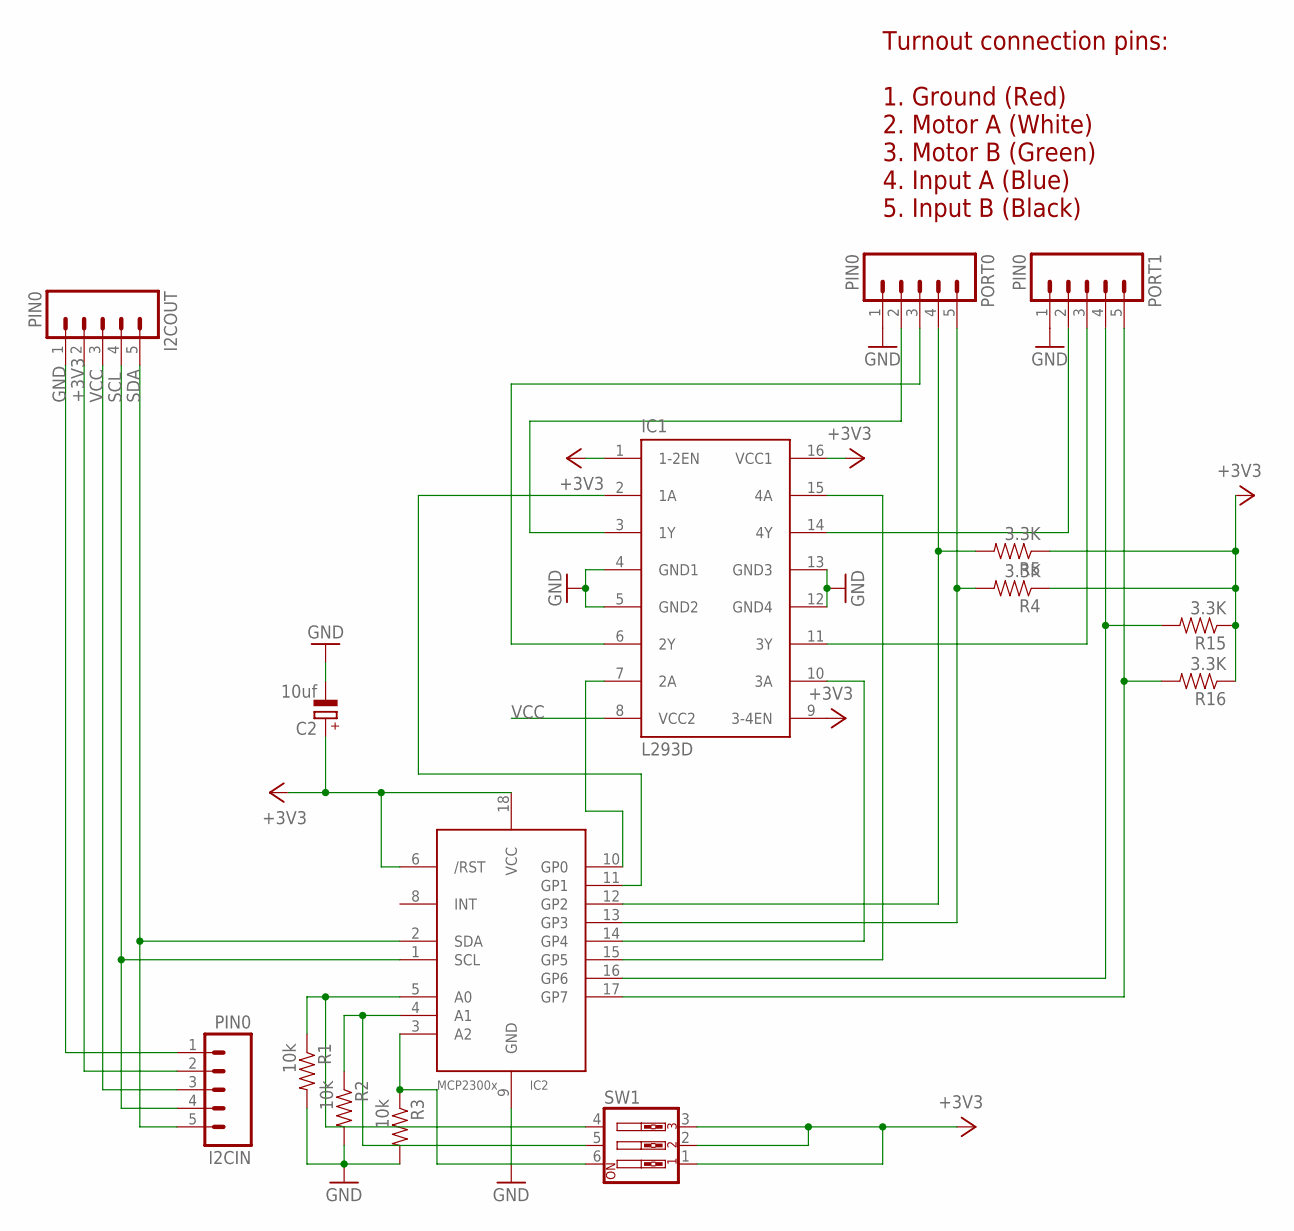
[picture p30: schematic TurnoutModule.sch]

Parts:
C2: 10uf; E2,5-6
I2CIN, I2COUT: PIN0; 05P
IC1: L293D; DIL16
IC2: MCP23008/P; DIL18
PORT0, PORT1: PIN0; 05P
R1, R2, R3: 10k; AXIAL-0.4
R4, R5, R15, R16: 3.3K; AXIAL-0.4
SW1: SW_DIP-3; EDG-03

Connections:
+3V3: C2.+, I2CIN.2, I2COUT.2, IC1.1 (1-2EN), IC1.9 (3-4EN), IC1.16 (VCC1), IC2.6 (/RST), IC2.18 (VCC), R4.P$1 (1), R5.P$1 (1), R15.P$1 (1), R16.P$1 (1), SW1.1, SW1.2, SW1.3
GND: C2.-, I2CIN.1, I2COUT.1, IC1.4 (GND1), IC1.5 (GND2), IC1.12 (GND4), IC1.13 (GND3), IC2.9 (GND), PORT0.1, PORT1.1, R1.P$2 (2), R2.P$2 (2), R3.P$2 (2)
unnamed: IC2.5 (A0), R1.P$1 (1), SW1.4
unnamed: IC2.17 (GP7), PORT1.5, R16.P$2 (2)
unnamed: IC1.3 (1Y), PORT0.2
unnamed: IC2.4 (A1), R2.P$1 (1), SW1.5
unnamed: IC2.16 (GP6), PORT1.4, R15.P$2 (2)
unnamed: IC1.6 (2Y), PORT0.3
unnamed: IC2.3 (A2), R3.P$1 (1), SW1.6
unnamed: IC1.7 (2A), IC2.10 (GP0)
unnamed: IC1.2 (1A), IC2.11 (GP1)
unnamed: IC1.14 (4Y), PORT1.2
unnamed: IC2.12 (GP2), PORT0.4, R5.P$2 (2)
unnamed: IC1.11 (3Y), PORT1.3
unnamed: IC1.10 (3A), IC2.14 (GP4)
unnamed: IC1.15 (4A), IC2.15 (GP5)
unnamed: IC2.13 (GP3), PORT0.5, R4.P$2 (2)
SCL: I2CIN.4, I2COUT.4, IC2.1 (SCL)
SDA: I2CIN.5, I2COUT.5, IC2.2 (SDA)
VCC: I2CIN.3, I2COUT.3, IC1.8 (VCC2)

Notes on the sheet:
Turnout connection pins: 1. Ground (Red) 2. Motor A (White) 3. Motor B (Green) 4. Input A (Blue) 5. Input B (Black)

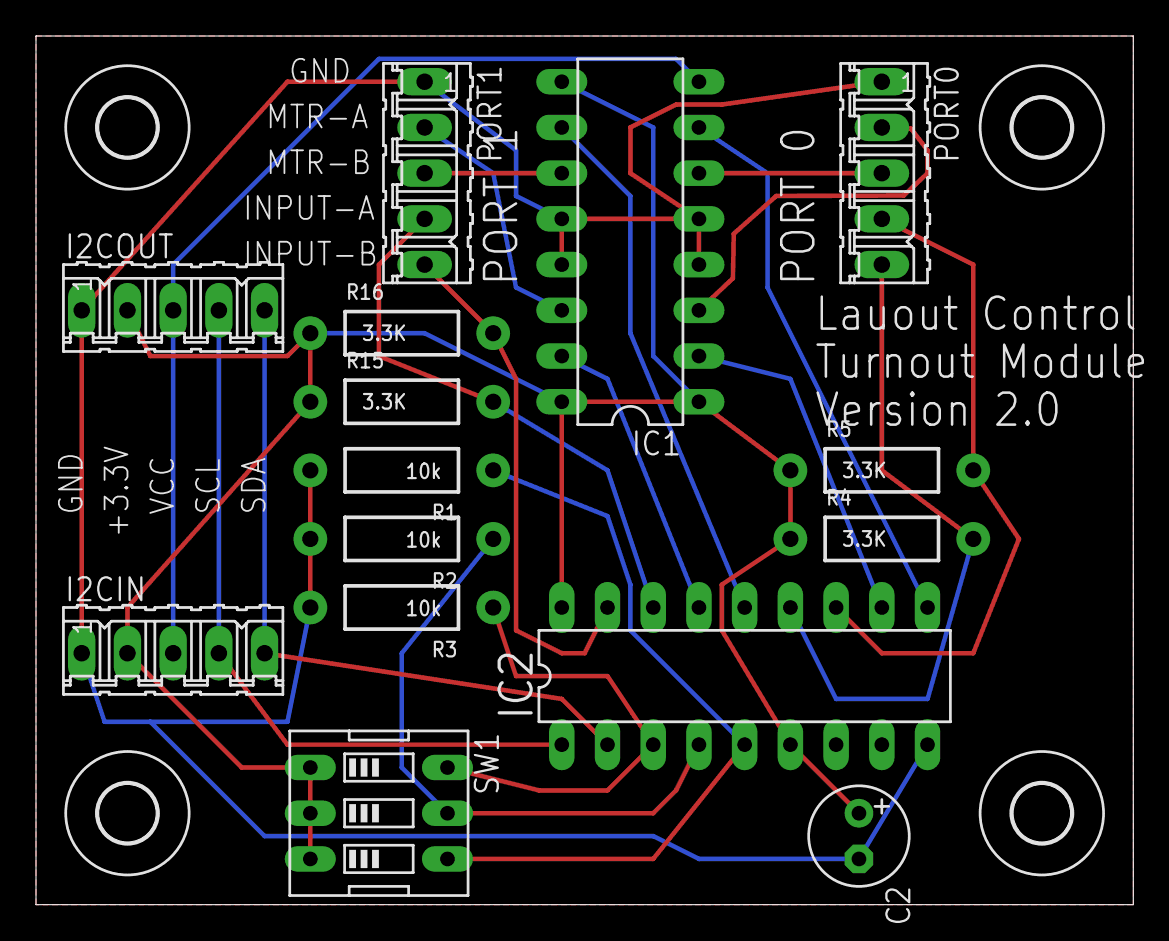
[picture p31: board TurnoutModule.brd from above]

Board: 2 copper layers, 61.0 x 48.3 mm, 19 parts (0 on the bottom side), 20 nets.

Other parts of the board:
U$2, U$3, U$4, U$5: 3,2

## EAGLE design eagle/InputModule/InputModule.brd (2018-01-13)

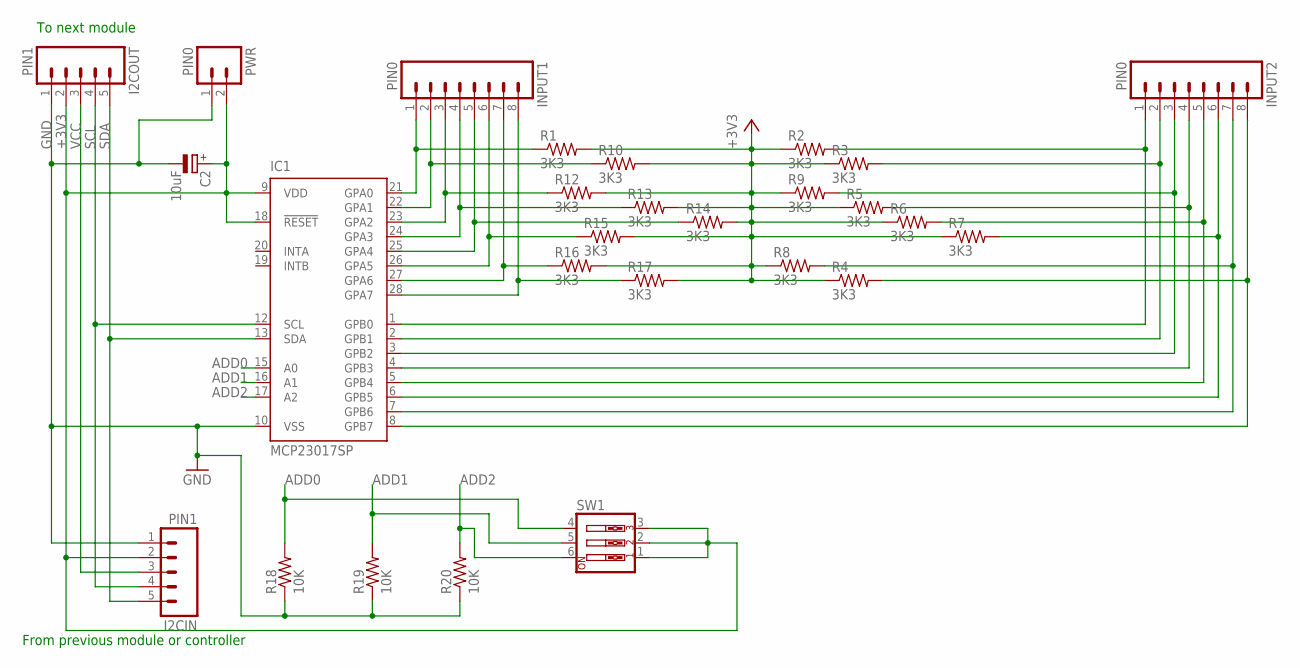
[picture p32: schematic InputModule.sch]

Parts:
C2: 10uF; E2,5-6
I2CIN, I2COUT: PIN1; 05P
IC1: MCP23017SP; DIL28-3
INPUT1, INPUT2: PIN0; 1X08_ROUND
PWR: PIN0; 02P
R1, R2, R3, R4, R5, R6, R7, R8, R9, R10, R12, R13, R14, R15, R16, R17: 3K3; AXIAL-0.4
R18, R19, R20: 10K; AXIAL-0.4
SW1: SW_DIP-3; EDG-03

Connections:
+3V3: C2.+, I2CIN.2, I2COUT.2, IC1.9 (VDD), IC1.18 (!RESET), PWR.2, R1.P$2 (2), R2.P$1 (1), R3.P$1 (1), R4.P$1 (1), R5.P$1 (1), R6.P$1 (1), R7.P$1 (1), R8.P$1 (1), R9.P$1 (1), R10.P$2 (2), R12.P$2 (2), R13.P$2 (2), R14.P$2 (2), R15.P$2 (2), R16.P$2 (2), R17.P$2 (2), SW1.1, SW1.2, SW1.3
ADD0: IC1.15 (A0), R18.P$2 (2), SW1.4
ADD1: IC1.16 (A1), R19.P$2 (2), SW1.5
ADD2: IC1.17 (A2), R20.P$2 (2), SW1.6
GND: C2.-, I2CIN.1, I2COUT.1, IC1.10 (VSS), PWR.1, R18.P$1 (1), R19.P$1 (1), R20.P$1 (1)
unnamed: IC1.1 (GPB0), INPUT2.1, R2.P$2 (2)
unnamed: IC1.2 (GPB1), INPUT2.2, R3.P$2 (2)
unnamed: IC1.3 (GPB2), INPUT2.3, R9.P$2 (2)
unnamed: IC1.4 (GPB3), INPUT2.4, R5.P$2 (2)
unnamed: IC1.5 (GPB4), INPUT2.5, R6.P$2 (2)
unnamed: IC1.6 (GPB5), INPUT2.6, R7.P$2 (2)
unnamed: IC1.7 (GPB6), INPUT2.7, R8.P$2 (2)
unnamed: IC1.8 (GPB7), INPUT2.8, R4.P$2 (2)
unnamed: IC1.21 (GPA0), INPUT1.1, R1.P$1 (1)
unnamed: IC1.22 (GPA1), INPUT1.2, R10.P$1 (1)
unnamed: IC1.23 (GPA2), INPUT1.3, R12.P$1 (1)
unnamed: IC1.24 (GPA3), INPUT1.4, R13.P$1 (1)
unnamed: IC1.25 (GPA4), INPUT1.5, R14.P$1 (1)
unnamed: IC1.26 (GPA5), INPUT1.6, R15.P$1 (1)
unnamed: IC1.27 (GPA6), INPUT1.7, R16.P$1 (1)
unnamed: IC1.28 (GPA7), INPUT1.8, R17.P$1 (1)
SCL: I2CIN.4, I2COUT.4, IC1.12 (SCL)
SDA: I2CIN.5, I2COUT.5, IC1.13 (SDA)
VCC: I2CIN.3, I2COUT.3

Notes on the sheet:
From previous module or controller
To next module

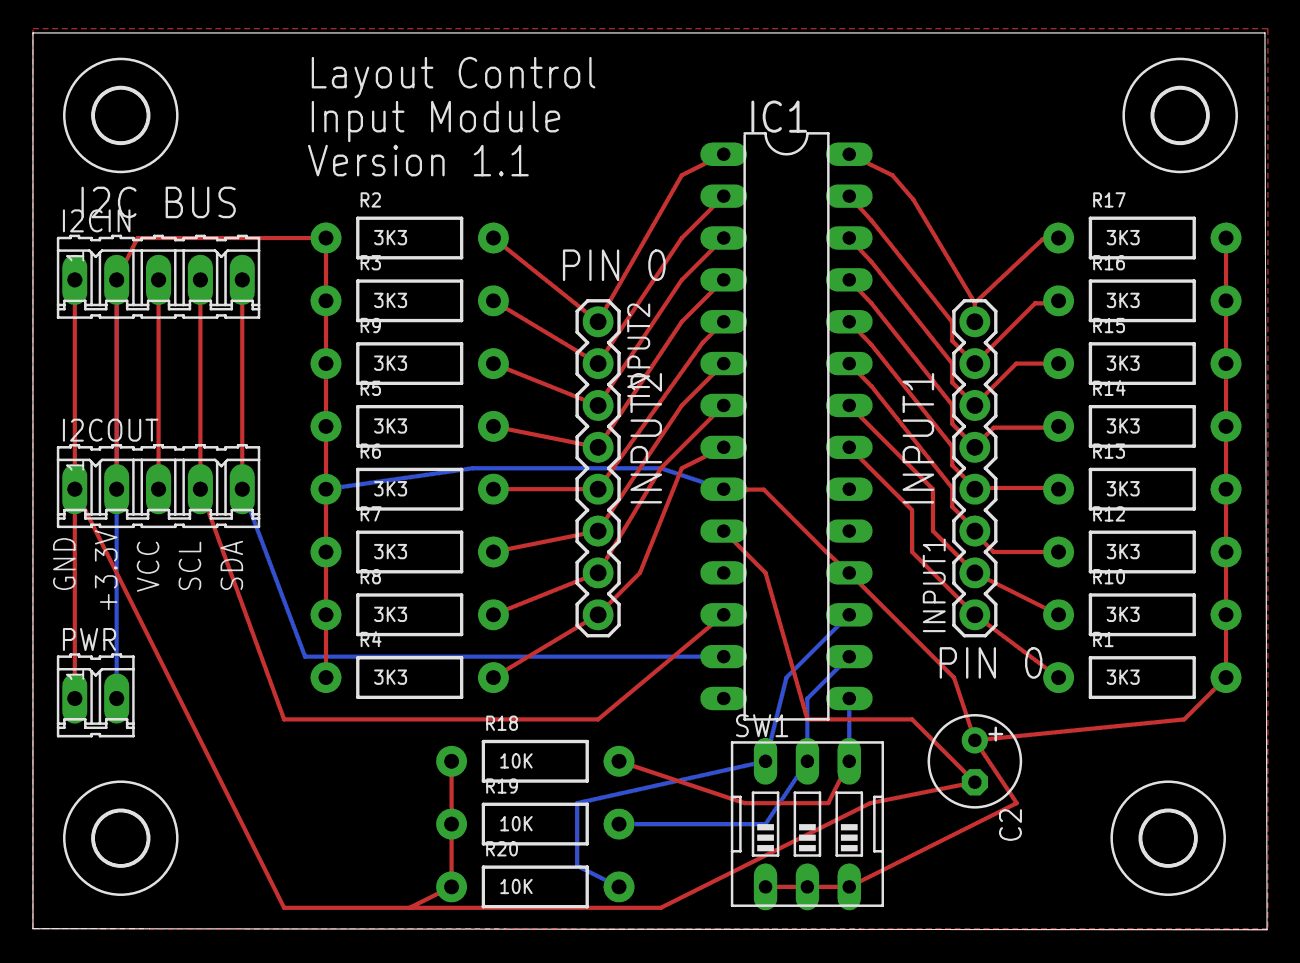
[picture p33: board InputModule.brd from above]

Board: 2 copper layers, 74.9 x 54.4 mm, 31 parts (0 on the bottom side), 24 nets.

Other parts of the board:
U$1, U$2, U$3, U$4: 3,2

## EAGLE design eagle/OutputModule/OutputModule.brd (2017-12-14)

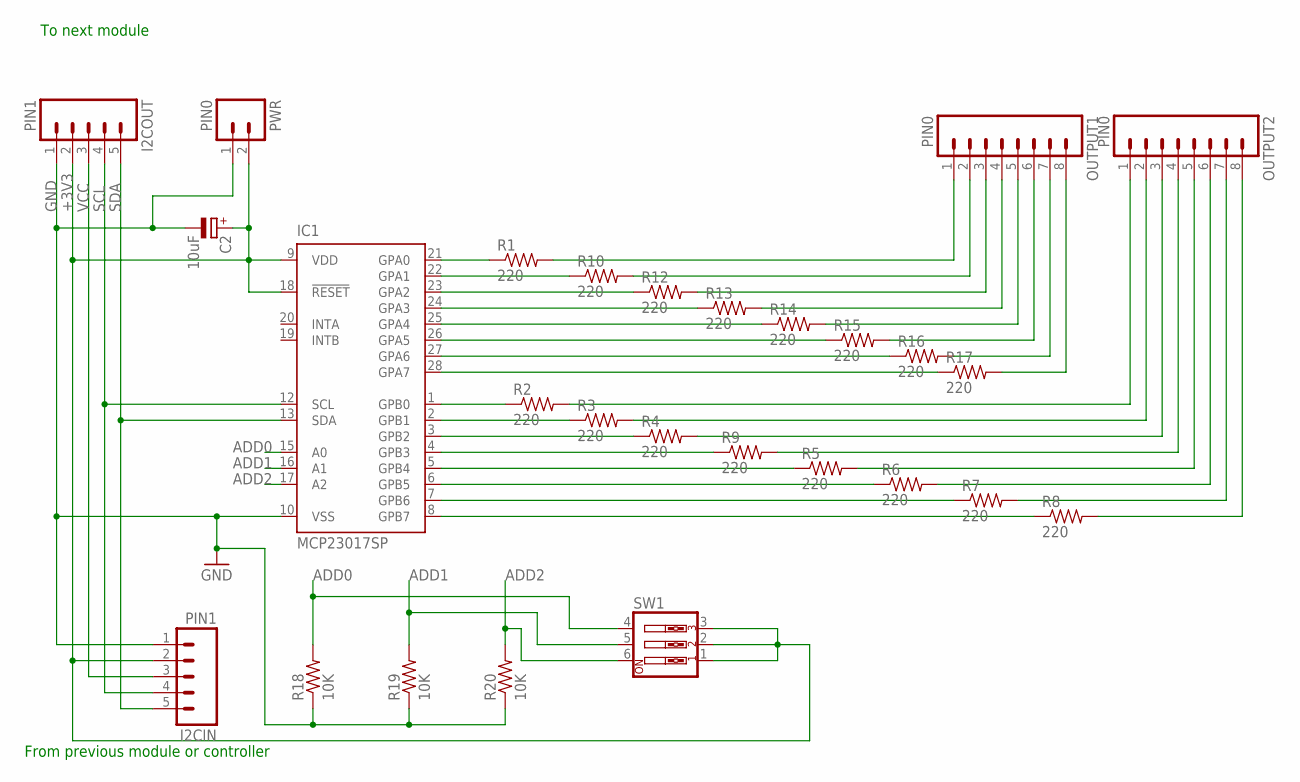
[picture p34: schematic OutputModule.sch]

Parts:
C2: 10uF; E2,5-6
I2CIN, I2COUT: PIN1; 05P
IC1: MCP23017SP; DIL28-3
OUTPUT1, OUTPUT2: PIN0; 1X08_ROUND
PWR: PIN0; 02P
R1, R2, R3, R4, R5, R6, R7, R8, R9, R10, R12, R13, R14, R15, R16, R17: 220; AXIAL-0.4
R18, R19, R20: 10K; AXIAL-0.4
SW1: SW_DIP-3; EDG-03

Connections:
+3V3: C2.+, I2CIN.2, I2COUT.2, IC1.9 (VDD), IC1.18 (!RESET), PWR.2, SW1.1, SW1.2, SW1.3
ADD0: IC1.15 (A0), R18.P$2 (2), SW1.4
ADD1: IC1.16 (A1), R19.P$2 (2), SW1.5
ADD2: IC1.17 (A2), R20.P$2 (2), SW1.6
GND: C2.-, I2CIN.1, I2COUT.1, IC1.10 (VSS), PWR.1, R18.P$1 (1), R19.P$1 (1), R20.P$1 (1)
unnamed: OUTPUT2.7, R7.P$2 (2)
unnamed: OUTPUT2.1, R2.P$2 (2)
unnamed: OUTPUT2.2, R3.P$2 (2)
unnamed: OUTPUT2.3, R4.P$2 (2)
unnamed: OUTPUT2.4, R9.P$2 (2)
unnamed: OUTPUT2.5, R5.P$2 (2)
unnamed: OUTPUT1.8, R17.P$2 (2)
unnamed: OUTPUT1.7, R16.P$2 (2)
unnamed: IC1.1 (GPB0), R2.P$1 (1)
unnamed: IC1.2 (GPB1), R3.P$1 (1)
unnamed: IC1.3 (GPB2), R4.P$1 (1)
unnamed: IC1.5 (GPB4), R5.P$1 (1)
unnamed: IC1.6 (GPB5), R6.P$1 (1)
unnamed: IC1.7 (GPB6), R7.P$1 (1)
unnamed: IC1.8 (GPB7), R8.P$1 (1)
unnamed: OUTPUT2.6, R6.P$2 (2)
unnamed: IC1.4 (GPB3), R9.P$1 (1)
unnamed: OUTPUT2.8, R8.P$2 (2)
unnamed: IC1.21 (GPA0), R1.P$1 (1)
unnamed: IC1.22 (GPA1), R10.P$1 (1)
unnamed: IC1.23 (GPA2), R12.P$1 (1)
unnamed: IC1.24 (GPA3), R13.P$1 (1)
unnamed: IC1.25 (GPA4), R14.P$1 (1)
unnamed: IC1.26 (GPA5), R15.P$1 (1)
unnamed: IC1.27 (GPA6), R16.P$1 (1)
unnamed: IC1.28 (GPA7), R17.P$1 (1)
unnamed: OUTPUT1.6, R15.P$2 (2)
unnamed: OUTPUT1.5, R14.P$2 (2)
unnamed: OUTPUT1.4, R13.P$2 (2)
unnamed: OUTPUT1.3, R12.P$2 (2)
unnamed: OUTPUT1.2, R10.P$2 (2)
unnamed: OUTPUT1.1, R1.P$2 (2)
SCL: I2CIN.4, I2COUT.4, IC1.12 (SCL)
SDA: I2CIN.5, I2COUT.5, IC1.13 (SDA)
VCC: I2CIN.3, I2COUT.3

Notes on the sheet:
From previous module or controller
To next module

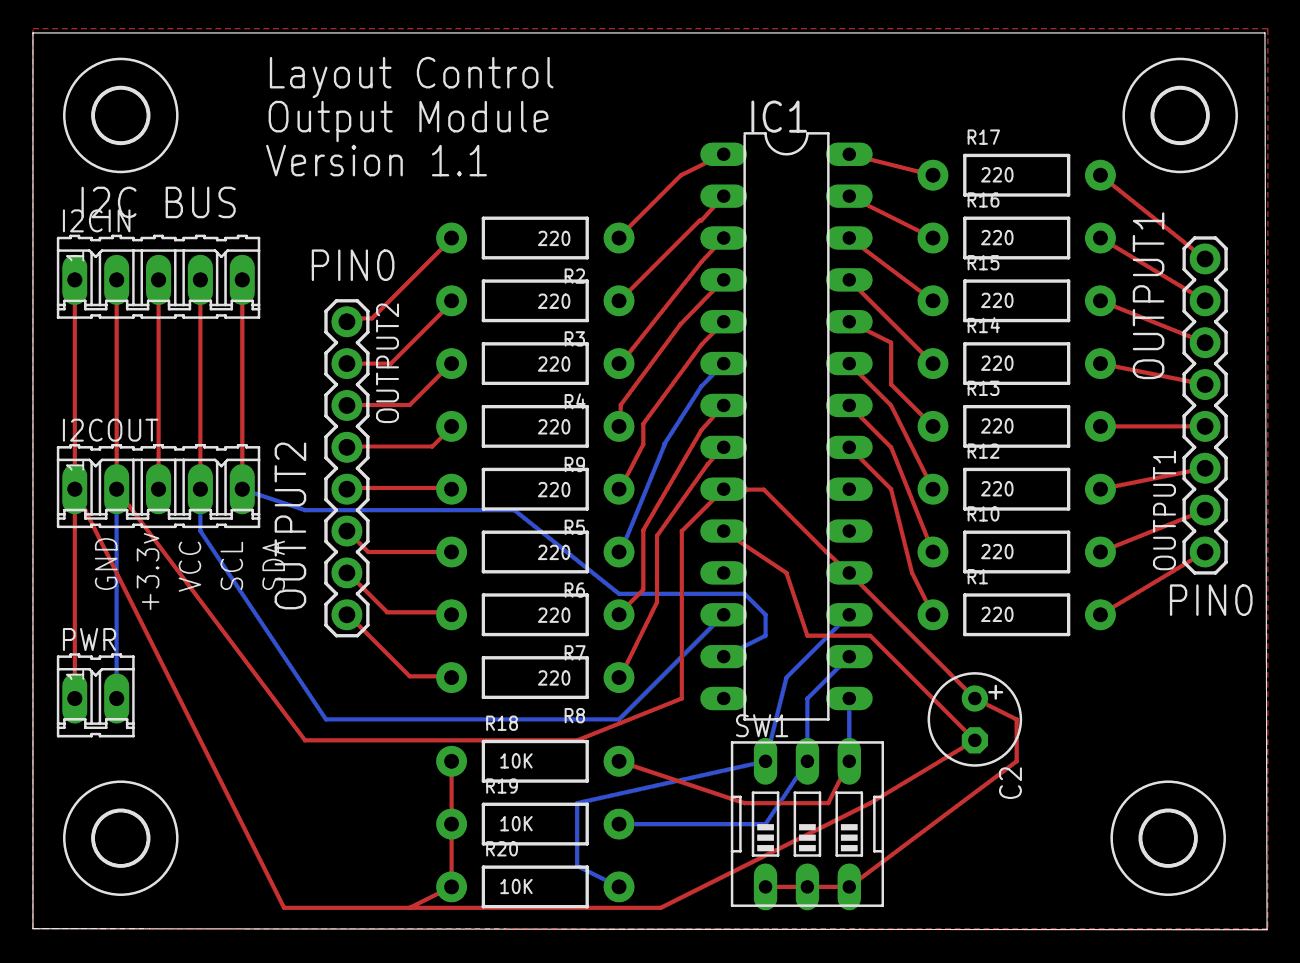
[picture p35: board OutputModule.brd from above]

Board: 2 copper layers, 74.9 x 54.4 mm, 31 parts (0 on the bottom side), 40 nets.

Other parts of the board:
U$1, U$2, U$3, U$4: 3,2

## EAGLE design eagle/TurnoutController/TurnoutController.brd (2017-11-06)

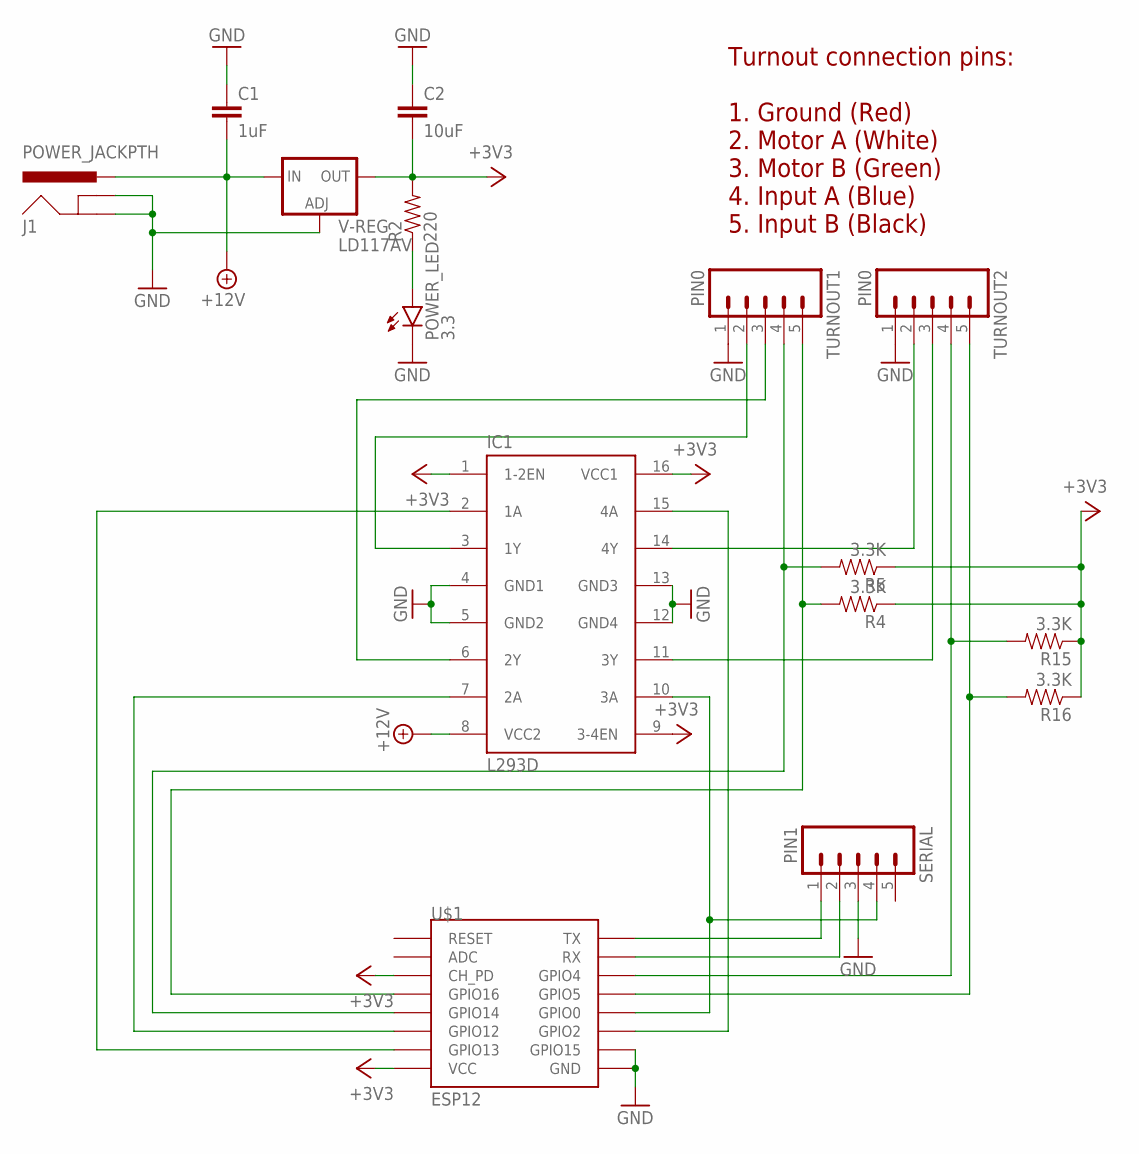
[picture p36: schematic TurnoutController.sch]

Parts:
C1: 1uF; CAP-PTH-SMALL
C2: 10uF; CAP-PTH-SMALL
IC1: L293D; DIL16
J1: POWER_JACKPTH; POWER_JACK_PTH
POWER_LED: 3.3; LED5MM
R2: 220; AXIAL-0.4
R4, R5, R15, R16: 3.3K; AXIAL-0.4
SERIAL: PIN1; 05P
TURNOUT1, TURNOUT2: PIN0; 05P
U$1: ESP12
V-REG: LD117AV; TO220L1

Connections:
+3V3: C2.2, IC1.1 (1-2EN), IC1.9 (3-4EN), IC1.16 (VCC1), R2.P$2 (2), R4.P$1 (1), R5.P$1 (1), R15.P$1 (1), R16.P$1 (1), U$1.CH_PD, U$1.VCC, V-REG.2 (OUT)
+12V: C1.2, IC1.8 (VCC2), J1.PWR, V-REG.3 (IN)
GND: C1.1, C2.1, IC1.4 (GND1), IC1.5 (GND2), IC1.12 (GND4), IC1.13 (GND3), J1.GND, J1.GNDBREAK, POWER_LED.K (C), SERIAL.3, TURNOUT1.1, TURNOUT2.1, U$1.GND, U$1.GPIO15, V-REG.1 (ADJ)
unnamed: R16.P$2 (2), TURNOUT2.5, U$1.GPIO5
unnamed: IC1.3 (1Y), TURNOUT1.2
unnamed: SERIAL.1, U$1.TX
unnamed: R15.P$2 (2), TURNOUT2.4, U$1.GPIO4
unnamed: IC1.6 (2Y), TURNOUT1.3
unnamed: POWER_LED.A, R2.P$1 (1)
unnamed: IC1.7 (2A), U$1.GPIO12
unnamed: IC1.2 (1A), U$1.GPIO13
unnamed: IC1.14 (4Y), TURNOUT2.2
unnamed: SERIAL.2, U$1.RX
unnamed: R5.P$2 (2), TURNOUT1.4, U$1.GPIO14
unnamed: IC1.11 (3Y), TURNOUT2.3
unnamed: IC1.10 (3A), SERIAL.4, U$1.GPIO0
unnamed: IC1.15 (4A), U$1.GPIO2
unnamed: R4.P$2 (2), TURNOUT1.5, U$1.GPIO16

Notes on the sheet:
Turnout connection pins: 1. Ground (Red) 2. Motor A (White) 3. Motor B (Green) 4. Input A (Blue) 5. Input B (Black)

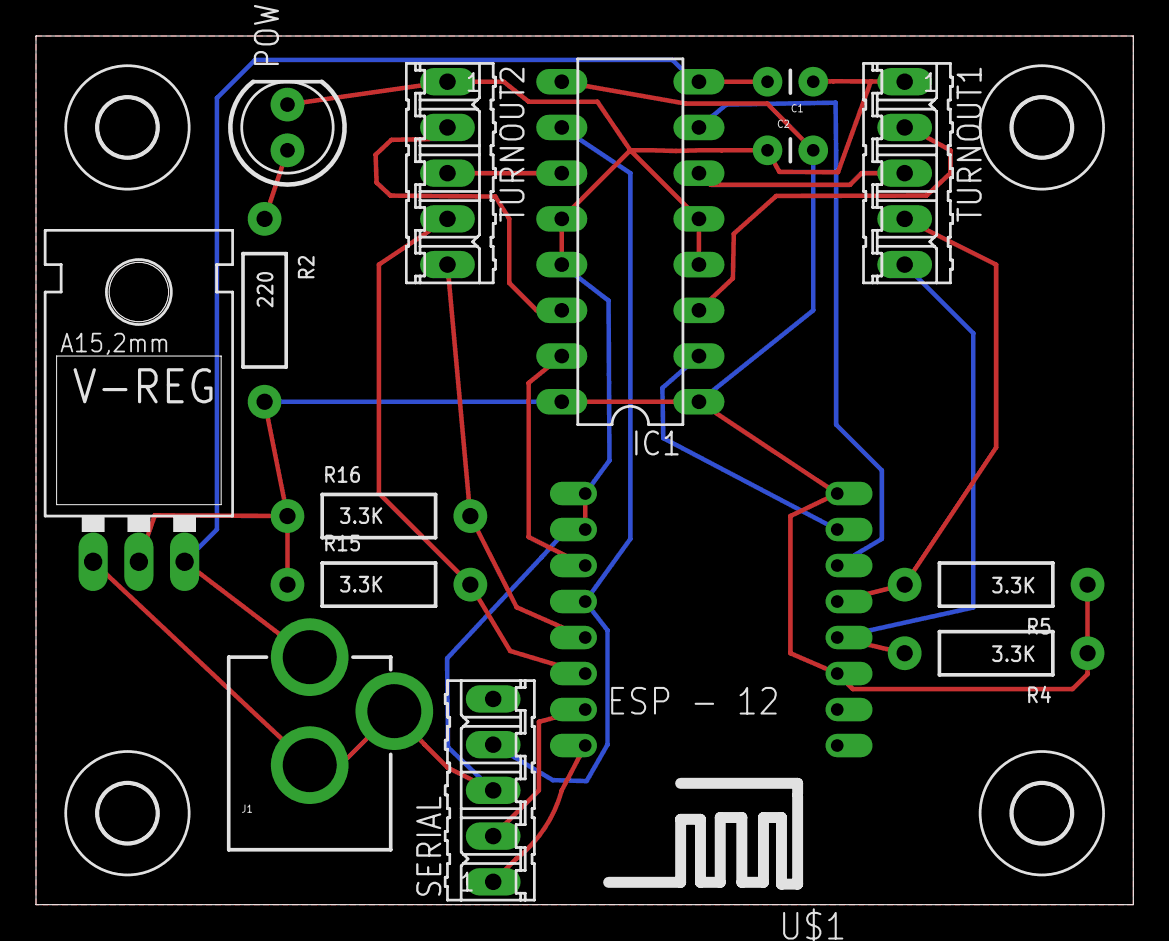
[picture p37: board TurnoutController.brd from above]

Board: 2 copper layers, 61.0 x 48.3 mm, 19 parts (0 on the bottom side), 18 nets.

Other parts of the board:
U$2, U$3, U$4, U$5: 3,2

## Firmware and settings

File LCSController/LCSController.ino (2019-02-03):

// Required ESP/Arduino includes
#include <dummy.h>
#include <Wire.h>
#include <EEPROM.h>
#include <FS.h>
#include <ArduinoJson.h>
#include <ESP8266WiFi.h>
#include <ESP8266HTTPClient.h>
#include <ESP8266httpUpdate.h>
#include <WiFiUdp.h>
#include <WiFiClient.h>

#include "UDPMessage.h"

// Main controller files
#include "Controller.h"
#include "GlobalDefs.h"
#include "NetworkManager.h"

// Modules
#include "TurnoutModule.h"
#include "InputModule.h"
#include "OutputModule.h"

// Devices
#include "TurnoutDevice.h"
#include "PanelOutputDevice.h"
#include "PanelInputDevice.h"
#include "SignalDevice.h"
#include "SemaphoreDevice.h"
#include "BlockDevice.h"

struct DeviceConfigStruct
{
	byte deviceClass;
	byte port;
	int deviceID;
};
typedef struct DeviceConfigStruct DeviceConfigStruct;

struct ModuleConfigStruct
{
	byte moduleClass;
	byte address;
	byte deviceCount;
	DeviceConfigStruct devices[MAX_DEVICES];
};
typedef struct ModuleConfigStruct ModuleConfigStruct;

struct ControllerConfigStruct
{
	ModuleConfigStruct modules[MAX_MODULES];
};
typedef struct ControllerConfigStruct ControllerConfigStruct;

// STATUS_LED_PIN is used to show the status of the connection to the WiFi network
// LED on indicates the controller is connected
// LED off indicates the controller is offline
const byte STATUS_LED_PIN = 2;// use the built in blue LED on the ESP8266 connected to pin2
const byte LOCKOUT_PIN = 13;
const byte CONFIG_VERSION = 1;
bool lockout = false;
byte lastLockoutRead = 0;
long currentLockoutTimeout = 0;

bool downloadConfigFlag = false;

ControllerClassEnum controllerClass = ControllerUnknown;
int controllerID = 0;
byte moduleCount = 0;

Controller controller(LocalServerPort);
String jsonTextToSave;
int nextModuleToNotify = -1;
Module *modules[MAX_MODULES];
StaticJsonBuffer<2048> jsonBuffer;

void setup() 
{
	Serial.begin(115200);
#ifdef PROJECT_DEBUG
	Serial.println("-------------------------------------------------");
	Serial.printf("LCS Controller Version: %d.%d.%d\n\n", MajorVersion, MinorVersion, BuildVersion);
	Serial.print("DEBUG BUILD STARTING.  Available RAM: ");
	Serial.println(ESP.getFreeHeap());
	Serial.println("-------------------------------------------------");
#else
	Serial.println();
	Serial.println();
	Serial.println("-------------------------------------------------");
	Serial.printf("LCS Controller Version: %d.%d.%d\n\n", MajorVersion, MinorVersion, BuildVersion);
	Serial.print("Available RAM: ");
	Serial.println(ESP.getFreeHeap());
	Serial.printf("Serial Number: %d\n\n", ESP.getChipId());
	Serial.println("-------------------------------------------------");
#endif
	DEBUG_PRINT("setup\n");
	EEPROM.begin(128);
	DEBUG_PRINT("SPIFFS SIZE %d REAL SIZE %d  ID %d\n", ESP.getFlashChipSize(), ESP.getFlashChipRealSize(), ESP.getFlashChipId());
	bool result = SPIFFS.begin();
	DEBUG_PRINT("SPIFFS opened: %d\n", result);
	
	memset(modules, 0, sizeof(Module*)*MAX_MODULES);
	ControllerConfigStruct controllerConfig;
	memset(&controllerConfig, 0, sizeof(ControllerConfigStruct));

	loadControllerConfiguration(&controllerConfig);

	setupHardware();

	if (downloadConfigFlag == false)
		createModules(&controllerConfig);

	controller.setServerFoundCallback(serverFound);
	controller.setSendStatusCallback(sendStatusMessage);
	controller.setup((ControllerClassEnum)controllerClass, controllerID);

	for (byte x = 0; x <moduleCount; x++)
	{
		Module *module = modules[x];

		if (module)
		{
			if (controllerClass == ControllerMulti)
			{
				module->finishSetupWire();
			}
			else
			{
				module->finishSetupNoWire();
			}
		}
	}

	NetManager.setUdpMessageCallback(udpMessageCallback);
	NetManager.setWIFIConnectCallback(networkConnected);
	NetManager.setNotificationListChangedCallback(notificationListChanged);
	NetManager.init(8080, controllerID);

	DEBUG_PRINT("setup complete\n");
}
void serverFound(void)
{
	DEBUG_PRINT("serverFound\n");

	if (downloadConfigFlag)
	{
		downloadConfig();
	}
	for (byte x = 0; x < moduleCount; x++)
	{
		Module *module = modules[x];
		if (module)
		{
			UDPMessage outMessage;
			outMessage.setMessageID(DEVICE_STATUS);
			outMessage.setID(module->getAddress());
			byte count = 0;
			for (byte index = 0; index < MAX_DEVICES; index++)
			{
				if (count >= 8)
				{
					NetManager.sendUdpMessage(outMessage, true);
					outMessage = UDPMessage();
					outMessage.setMessageID(DEVICE_STATUS);
					outMessage.setID(module->getAddress());
					count = 0;
				}
				Device *device = module->getDevice(index);
				if (device)
				{
					device->serverFound(outMessage, count);
				}
			}
			if (count > 0)
			{
				NetManager.sendUdpMessage(outMessage, true);
			}
		}
	}
	DEBUG_PRINT("serverFound COMPLETE\n");
}

void networkConnected(bool connected)
{
	DEBUG_PRINT("networkConnected: %s\n", connected ? "CONNECTED" : "DISCONNECTED");
	if (connected)
		controller.networkOnline();
	else
		controller.networkOffline();

	for (byte x = 0; x < moduleCount; x++)
	{
		Module *module = modules[x];
		if (module)
		{
			for (byte index = 0; index < MAX_DEVICES; index++)
			{
				Device *device = module->getDevice(index);
				if (device)
				{
					if (connected)
						device->networkOnline();
					else
						device->networkOffline();
				}
			}
			module->sendStatusMessage();
		}
	}
}

void udpMessageCallback(const UDPMessage &message)
{
	DEBUG_PRINT("udpMessageCallback: %d\n", message.getMessageID());
	controller.processMessage(message);
	for (byte x = 0; x < moduleCount; x++)
	{
		Module *module = modules[x];
		if (module)
		{
			if (controllerClass == ControllerMulti)
				module->processUDPMessageWire(message);
			else
				module->processUDPMessageNoWire(message);
		}
	}
}

void setupHardware(void)
{
	DEBUG_PRINT("Setup Hardware: %d\n", controllerClass);
	if (controllerClass == ControllerMulti)
	{
		Wire.begin(4, 5); //creates a Wire object

		//Pin 12 is the network status indicator LED
		// ON - Connected to the server
		// OFF - Disconnected
		pinMode(STATUS_LED_PIN, OUTPUT);
		digitalWrite(STATUS_LED_PIN, HIGH);
		//Pin 13 is the lockout switch input
		pinMode(LOCKOUT_PIN, INPUT);
	}
}

void loop() 
{
	checkLockoutPin();
	NetManager.process();
	controller.process();

	for (byte x = 0; x < moduleCount; x++)
	{
		if (controllerClass == ControllerMulti)
		{
			if (modules[x])
				modules[x]->processWire();
		}
		else
		{
			if (modules[x])
				modules[x]->processNoWire();
		}
	}

	if (controllerClass == ControllerMulti)
		setStatusIndicator();

	if (jsonTextToSave.length() > 0)
	{
		saveControllerConfig(jsonTextToSave, false);
		jsonTextToSave = "";
	}

	if (nextModuleToNotify >= 0)
	{
		Module *m = modules[nextModuleToNotify++];
		if (m)
			m->sendStatusMessage();
		if (nextModuleToNotify >= moduleCount)
			nextModuleToNotify = -1;
	}
	if (moduleCount == 0)
		delay(100);
	else
		delay(50);
}

String getConfiguration(void)
{
	DEBUG_PRINT("GET CONTROLLER CONFIGURATION\n");
	String json;
	String fileName("/ControllerConfig.json");
	File f = SPIFFS.open(fileName, "r");

	if (f)
	{
		json = f.readString();
		DEBUG_PRINT("Configuration  LENGTH: %d:\n%s\n", json.length(), json.c_str());
		f.close();
	}
	else
	{
		DEBUG_PRINT("Configuration file %s is missing or can not be opened.  Initializing to 0\n", fileName.c_str());
	}
	return json;
}

void loadControllerConfiguration(struct ControllerConfigStruct *config)
{
	DEBUG_PRINT("LOAD CONTROLLER CONFIGURATION\n");
	String json(getConfiguration());

	if (json.length() > 0)
	{
		if (parseControllerConfig(json, true, config) == false)
		{
			DEBUG_PRINT("SETTING DOWLOADFLAG TO TRUE\n");
			downloadConfigFlag = true;
		}
	}
	else
	{
		DEBUG_PRINT("SETTING DOWLOADFLAG TO TRUE\n");
		downloadConfigFlag = true;
	}
}

void loadModuleConfiguration(byte address, struct ModuleConfigStruct *config)
{
	DEBUG_PRINT("LOAD MODULE CONFIGURATION.  ADDRESS: %d\n", address);
	String json;
	String fileName("/ModuleConfig_");
	fileName += address;
	fileName += ".json";
	File f = SPIFFS.open(fileName, "r");

	if (f)
	{
		json = f.readString();
		DEBUG_PRINT("Configuration:\n%s\n", json.c_str());
		f.close();
	}
	else
	{
		DEBUG_PRINT("Configuration file %s is missing or can not be opened.  Initializing to 0\n", fileName.c_str());
	}

	if (json.length() > 0)
	{
		parseModuleConfig(json, config);
	}
	else
	{
//		downloadConfigFlag = true;
	}
}

void createDevices(struct ModuleConfigStruct *moduleConfig, Module *module)
{
	DEBUG_PRINT("CreateDevices.  Device Count: %d\n", moduleConfig->deviceCount);

	if (module)
	{
		for (byte x = 0; x < moduleConfig->deviceCount; x++)
		{
			Device *device = NULL;
			switch (moduleConfig->devices[x].deviceClass)
			{
				case DeviceTurnout:
				{
					DEBUG_PRINT("CreateDevices:  Creating Turnout Device\n");
					device = new TurnoutDevice();
					break;
				}
				case DeviceBlock:
				{
					DEBUG_PRINT("CreateDevices:  Creating Block Device\n");
					device = new BlockDevice();
					break;
				}
				case DeviceSignal:
				{
					DEBUG_PRINT("CreateDevices:  Creating Signal Device\n");
					device = new SignalDevice();
					break;
				}
				case DeviceSemaphore:
				{
					DEBUG_PRINT("CreateDevices:  Creating Signal Device\n");
					device = new SemaphoreDevice();
					break;
				}
				case DevicePanelOutput:
				{
					DEBUG_PRINT("CreateDevices:  Creating PanelOutput Device\n");
					device = new PanelOutputDevice();
					break;
				}
				case DevicePanelInput:
				{
					DEBUG_PRINT("CreateDevices:  Creating PanelInput Device\n");
					device = new PanelInputDevice();
					break;
				}
				default:
				{
					DEBUG_PRINT("CreateDevices:  INVALID DEVICE CLASS: %d\n", moduleConfig->devices[x].deviceClass);
					break;
				}
			}
			if (device)
			{
				device->setup(moduleConfig->devices[x].deviceID, moduleConfig->devices[x].port);
				module->addDevice(x, device);
			}
		}
	}
}

void createModules(struct ControllerConfigStruct *controllerConfig)
{
	DEBUG_PRINT("CreateModules. Count: %d\n", moduleCount);
	for (byte x = 0; x < moduleCount; x++)
	{
		Module *module = NULL;
		loadModuleConfiguration(controllerConfig->modules[x].address, &controllerConfig->modules[x]);
		switch (controllerConfig->modules[x].moduleClass)
		{
			case ModuleSemaphore:
			case ModuleTurnout:
			{
				DEBUG_PRINT("createModules:  Creating Turnout Module address: %d\n", controllerConfig->modules[x].address);
				module = new TurnoutModule;
				break;
			}
			case ModuleInput:
			{
				DEBUG_PRINT("createModules:  Creating Input Module address: %d\n", controllerConfig->modules[x].address);
				module = new InputModule;
				break;
			}
			case ModuleOutput:
			{
				DEBUG_PRINT("createModules:  Creating Output Module address: %d\n", controllerConfig->modules[x].address);
				module = new OutputModule;
				break;
			}
			default:
			{
				DEBUG_PRINT("createModules:  INVALID MODULE CLASS: %d\n", controllerConfig->modules[x].moduleClass);
				break;
			}
		}
		modules[x] = module;
		if (module)
		{
			if (controllerClass == ControllerMulti)
				module->setupWire(controllerConfig->modules[x].address);
			else
				module->setupNoWire();
			createDevices(&controllerConfig->modules[x], module);
		}
	}
}

void downloadConfig(void)
{
	DEBUG_PRINT("downloadConfig\n");

	String payload = NetManager.getControllerConfig(ESP.getChipId());
	if (payload.length() > 0)
	{
		ControllerConfigStruct config;
		memset(&config, 0, sizeof(ControllerConfigStruct));
		if (parseControllerConfig(payload, false, &config))
		{
			downloadModuleConfigs(&config);
			downloadConfigFlag = false;
			saveControllerConfig(payload, true);
			controller.restart();
		}
	}
}

void downloadModuleConfigs(ControllerConfigStruct *config)
{
	for (byte x = 0; x < moduleCount; x++)
	{
		String json = NetManager.getModuleConfig(ESP.getChipId(), config->modules[x].address);
		if (json.length() > 0)
		{
			saveModuleConfig(json, config->modules[x].address);
		}
	}
}

bool parseControllerConfig(const String &jsonText, bool checkVersion, ControllerConfigStruct *config)
{
	DEBUG_PRINT("parseControllerConfig\n");
	jsonBuffer.clear();
	JsonObject &json = jsonBuffer.parseObject(jsonText);

	if (checkVersion && json["version"] != (int)CONFIG_VERSION)
	{
		DEBUG_PRINT("parseControllerConfig  WRONG VERSION.\n");
		return false;
	}

	controllerClass = (ControllerClassEnum)(int)json["controllerClass"];
	controllerID = json["controllerID"];

	if (controllerClass == ControllerUnknown)
	{
		DEBUG_PRINT("parseControllerConfig  INVALID CONTROLLER CLASS.\n");
		return false;
	}

	JsonArray &modules = json["modules"];
	moduleCount = modules.size();
	for (byte x = 0; x < modules.size(); x++)
	{
		JsonArray &devices = modules[x]["devices"];
		config->modules[x].moduleClass = modules[x]["class"];
		config->modules[x].address = modules[x]["address"];
	}

	JsonArray &notifications = json["controllersToNotify"];
	DEBUG_PRINT("parseControllerConfig:  Notification List size: %d\n", notifications.size());
	for (byte x = 0; x < notifications.size(); x++)
	{
		int id = notifications[x]["controllerID"];
		if (controllerID != id)
			NetManager.addNotificationController(id);
	}

	return true;
}

void parseModuleConfig(const String &jsonText, ModuleConfigStruct *config)
{
	DEBUG_PRINT("parseModuleConfig\n");
	jsonBuffer.clear();
	JsonObject &json = jsonBuffer.parseObject(jsonText);

	JsonArray &devices = json["devices"];
	config->deviceCount = devices.size();
	for (byte x = 0; x < devices.size(); x++)
	{
		config->devices[x].port = devices[x]["p"];
		config->devices[x].deviceClass = devices[x]["c"];
		config->devices[x].deviceID = devices[x]["id"];

		DEBUG_PRINT("Device Config  Class: %d  Port: %d\n", config->devices[x].deviceClass, config->devices[x].port);
	}
}

void saveControllerConfig(const String &jsonText, bool addVersion)
{
	DEBUG_PRINT("Saving controller configuration to file.  Total Modules: %d\n", moduleCount);
	String s;
	if (addVersion)
	{
		jsonBuffer.clear();
		JsonObject &json = jsonBuffer.parseObject(jsonText);

		json["version"] = (int)CONFIG_VERSION;
		json.printTo(s);
	}
	else
	{
		s = jsonText;
	}

	String fileName("/ControllerConfig.json");

	if (SPIFFS.exists(fileName))
		SPIFFS.remove(fileName);
	File f = SPIFFS.open(fileName, "w");

	if (f)
	{
		DEBUG_PRINT("Saving Controller config: %s\n", fileName.c_str());

//		DEBUG_PRINT("Updated Configuration with version:\n%s\n", s.c_str());
		f.write((const uint8_t *)s.c_str(), s.length());
		f.close();
	}
	else
	{
		DEBUG_PRINT("Saving controller config FAILED: %s  COULD NOT OPEN FILE\n", fileName.c_str());
	}
}

void saveModuleConfig(const String &jsonText, byte address)
{
	DEBUG_PRINT("Saving module configuration to file.\n");

	String fileName("/ModuleConfig_");
	fileName += address;
	fileName +=".json";

	if (SPIFFS.exists(fileName))
		SPIFFS.remove(fileName);
	File f = SPIFFS.open(fileName, "w");

	if (f)
	{
		DEBUG_PRINT("Saving module config: %s\n", fileName.c_str());

		//		DEBUG_PRINT("Updated Configuration with version:\n%s\n", s.c_str());
		f.write((const uint8_t *)jsonText.c_str(), jsonText.length());
		f.close();
	}
	else
	{
		DEBUG_PRINT("Saving module config FAILED: %s  COULD NOT OPEN FILE\n", fileName.c_str());
	}
}

void checkLockoutPin(void)
{
	long t = millis();
	byte current = digitalRead(LOCKOUT_PIN);
	if (current == lastLockoutRead)
	{
		if (current != lockout && (t - currentLockoutTimeout) > 250)
		{
			currentLockoutTimeout = t;
			lockout = current;
			for (byte x = 0; x < moduleCount; x++)
			{
				Module *module = modules[x];
				if (module)
				{
					for (byte index = 0; index < MAX_DEVICES; index++)
					{
						Device *device = module->getDevice(index);
						if (device)
							device->controllerLockout(lockout == LOW);
					}
				}
			}
		}
	}
	else
	{
		currentLockoutTimeout = t;
	}
	lastLockoutRead = current;
}

void sendStatusMessage(void)
{
	DEBUG_PRINT("sendStatusMessage\n");
	nextModuleToNotify = 0;
}

void notificationListChanged(const String &jsonText)
{
	StaticJsonBuffer<256> jsonBufferLocal;
	JsonArray &jsonArray = jsonBufferLocal.parseArray(jsonText);

	jsonBuffer.clear();
	JsonObject &json = jsonBuffer.parseObject(getConfiguration());

	DEBUG_PRINT("notificationListChanged  New Count: %d\n", jsonArray.size());
	json["controllersToNotify"] = jsonArray;
	json.printTo(jsonTextToSave);
	DEBUG_PRINT("NEW CONFIGURATION FILE:\n%s\n", jsonTextToSave.c_str());
}

void setStatusIndicator(void)
{
//	DEBUG_PRINT("setStatusIndicator: %d\n", NetManager.getWiFiConnected());
	if (NetManager.getWiFiConnected())
		digitalWrite(STATUS_LED_PIN, LOW); // Turn LED on
	else
		digitalWrite(STATUS_LED_PIN, HIGH); // Turn LED off
}

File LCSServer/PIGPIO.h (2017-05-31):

#ifndef PIGPIO_H
#define PIGPIO_H

#include <QObject>

#define PIN_IN  0
#define PIN_OUT 1

#define PIN_LOW  0
#define PIN_HIGH 1

#define MAX_PINS 41
#define MAX_MONITOR 5

class PIGPIO : public QObject
{
    Q_OBJECT
public:
    explicit PIGPIO(QObject *parent = 0);
    ~PIGPIO(void);

    bool pinDirection(int pin, int dir);
    int readPin(int pin);
    int pinWrite(int pin, int value);

signals:
    void pinChanged(int pin, int value);

public slots:
    void monitorPin(int pin);

protected slots:
    void timerProc(void);

private:
    bool exportPin(int pin);
    bool unExportPin(int pin);
    int m_pinList[MAX_PINS];
    int m_monitorList[MAX_MONITOR];
    int m_monitorValue[MAX_MONITOR];
};

#endif // PIGPIO_H

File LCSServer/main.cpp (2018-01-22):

#include <QCoreApplication>
#include <stdio.h>
#include <stdlib.h>
#include <QJsonObject>

#include "AppService.h"
#include "GlobalDefs.h"
#include "EntityMetadata.h"
#include "APIRequest.h"
#include "APIResponse.h"

void messageOutput(QtMsgType type, const QMessageLogContext &context, const QString &msg);
bool enableDebugMessages = false;

int main(int argc, char *argv[])
{
    bool startSimulator = false;
    EntityMetadata::instance();
    qInstallMessageHandler(messageOutput);
    qRegisterMetaType<ControllerStatusEnum>("ControllerStatusEnum");
    qRegisterMetaType<ControllerClassEnum>("ControllerClassEnum");
    qRegisterMetaType<DeviceClassEnum>("DeviceClassEnum");
    qRegisterMetaType<ModuleClassEnum>("ModuleClassEnum");
    qRegisterMetaType<NetActionType>("NetActionType");
    qRegisterMetaType<QJsonObject>();
    qRegisterMetaType<APIRequest>();

    QString name(QObject::tr("LCSServer"));
    QString description(QObject::tr("GCMRR Layout Control System (LCS)"));

    QString s;
    for(int x = 0; x < argc; x++)
    {
        QString s = QString(argv[x]);
        if(s == "-d" || s == "-D")
            enableDebugMessages = true;
        if(s == "-s" || s == "-S")
            startSimulator = true;
    }
    if(argc > 2 && s != "-c")
    {

        if(argc == 4)
        {
            QString s = QString(argv[2]);
            if(s != "-d")
            {
                name = argv[2];
                description = argv[3];
                argv[2][0] = '\0';
                argv[3][0] = '\0';
            }
        }
        else if(argc == 3)
        {
            QString s = QString(argv[2]);
            if(s != "-d")
            {
                name = argv[1];
                description = argv[2];
                argv[2][0] = '\0';
            }
        }
        else
        {
            qWarning(QObject::tr("Wrong number of parameters!\nUsage: LCSServer.exe [flags] [name description]").toLatin1());
            return 1;
        }
    }

    AppService service(argc, argv, name, description);

    if(startSimulator)
        service.startSimulator();

    return service.exec();
}

void messageOutput(QtMsgType type, const QMessageLogContext &context, const QString &msg)
{
    if(enableDebugMessages)
    {
        QByteArray localMsg = msg.toLocal8Bit();
        switch (type)
        {
        case QtDebugMsg:
            fprintf(stderr, "Debug: %s\n", localMsg.constData());
            break;
        case QtWarningMsg:
            fprintf(stderr, "Warning: %s (%s:%u, %s)\n", localMsg.constData(), context.file, context.line, context.function);
            break;
        case QtCriticalMsg:
            fprintf(stderr, "Critical: %s (%s:%u, %s)\n", localMsg.constData(), context.file, context.line, context.function);
            break;
        case QtFatalMsg:
            fprintf(stderr, "Fatal: %s (%s:%u, %s)\n", localMsg.constData(), context.file, context.line, context.function);
            abort();
        default:
            fprintf(stderr, "Info: %s (%s:%u, %s)\n", localMsg.constData(), context.file, context.line, context.function);
            break;
        }
    }
}

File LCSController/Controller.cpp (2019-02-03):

#include "Controller.h"
#include "GlobalDefs.h"
#include "NetworkManager.h"
#include "Local.h"
#include "DeviceMonitor.h"
#include "RouteMonitor.h"

#include <ESP8266WiFi.h>
#include <ESP8266HTTPClient.h>
#include <ESP8266httpUpdate.h>
#include <FS.h>
#define blinkingTimeout 200

Controller::Controller(int localServerPort)
	: m_class(ControllerUnknown), m_controllerID(-1)
{
}

Controller::~Controller()
{
}

// Be sure Controller::loadConfig() is called first!
// DO NOT call loadConfig from this function!!
void Controller::setup(ControllerClassEnum controllerClass, int controllerID)
{
	m_class = controllerClass;
	m_controllerID = controllerID;

	DEBUG_PRINT("------------------------\n");
	DEBUG_PRINT(" Serial #:     %d\r\n", ESP.getChipId());
	DEBUG_PRINT(" ControllerID: %d\r\n", m_controllerID);
	DEBUG_PRINT("------------------------\n");
}

void Controller::process(void)
{
}

void Controller::processMessage(const UDPMessage &message)
{
//	DEBUG_PRINT("NEW MESSAGE! MessageID %d  ID %d\n", message.getMessageID(), message.getID());

	// Let global objects process the message first
	Devices.processMessage(message);
	Routes.processMessage(message);

	if (message.getMessageID() == SYS_REBOOT_CONTROLLER && (message.getID() == 0 || message.getID() == ESP.getChipId()))
	{
		DEBUG_PRINT("REBOOT MESSAGE! Controller restarting.\n");
		restart();
	}
	else if (message.getMessageID() == SYS_DOWNLOAD_FIRMWARE && (message.getID() == 0 || message.getID() == ESP.getChipId()))
	{
		downloadFirmwareUpdate();
	}
	else if (message.getMessageID() == SYS_RESET_CONFIG && (message.getID() == 0 || message.getID() == ESP.getChipId()))
	{
		DEBUG_PRINT("RESET CONTROLLER CONFIG MESSAGE!\n");
		resetConfiguration();
		restart();
	}
	else if (message.getMessageID() == SYS_RESET_NOTIFICATION_LIST && (message.getID() == 0 || message.getID() == ESP.getChipId()))
	{
		DEBUG_PRINT("RESET NOTIFICATION LIST!\n");
		String json = NetManager.getNotificationList();
		NetManager.setNotificationList(json);
	}
	else if (message.getMessageID() == SYS_SERVER_SHUTDOWN)
	{
		DEBUG_PRINT("SERVER SHUTDOWN MESSAGE!\n");
		IPAddress address;
		NetManager.setServerAddress(address);
	}
	else if (message.getMessageID() == SYS_CONTROLLER_ONLINE)
	{
		DEBUG_PRINT("CONTROLLER ONLINE MESSAGE!  CONTROLLER %d\n", message.getID());
		IPAddress address(message.getField(0), message.getField(1), message.getField(2), message.getField(3));
		if (address != (uint32_t)0 && NetManager.updateNotificationList(message.getID(), address))
		{
			if (m_sendStatusCallback)
				m_sendStatusCallback();
		}
	}
	else if (message.getMessageID() == SYS_FIND_CONTROLLER && message.getID() == m_controllerID)
	{
		DEBUG_PRINT("FIND CONTROLLER MESSAGE.  LOOKING FOR ME!\n");
		IPAddress to(message.getField(0), message.getField(1), message.getField(2), message.getField(3));
		DEBUG_PRINT("FIND CONTROLLER MESSAGE.  LOOKING FOR ME!  SENDING MESSAGE TO: %s\n", to.toString().c_str());
		sendControllerOnlineMessage(to);
		if (m_sendStatusCallback)
			m_sendStatusCallback();
	}
	else if (message.getMessageID() == SYS_DEVICE_CONFIG_CHANGED)
	{
		DEBUG_PRINT("SYS_DEVICE_CONFIG_CHANGED. RESETTING NOTIFICATION LIST\n");
		String json = NetManager.getNotificationList();
		NetManager.setNotificationList(json);
	}
	else if (message.getMessageID() == SYS_SERVER_HEARTBEAT)
	{
		IPAddress address(message.getField(0), message.getField(1), message.getField(2), message.getField(3));
//		DEBUG_PRINT("SYS_SERVER_HEARTBEAT: %s\n", address.toString().c_str());
		// A 1 in field 4 indicates the server is just coming online
		if (address != NetManager.getServerAddress() || message.getField(4) == 1)
		{
			DEBUG_PRINT("SYS_SERVER_HEARTBEAT: %s  SAVING ADDRESS\n", address.toString().c_str());
			NetManager.setServerAddress(address);
			if (m_serverFoundCallback)
				m_serverFoundCallback();
			sendControllerOnlineMessage(address);
		}
	}
}

void Controller::downloadFirmwareUpdate(void)
{
	IPAddress address(NetManager.getServerAddress());
	int port(NetManager.getServerPort());

	if (WiFi.status() == WL_CONNECTED && port > 0)
	{
		// ControllerStatusFirmwareUpdate
		UDPMessage message;
		message.setMessageID(SYS_FIRMWARE_UPDATING);
		message.setID(ESP.getChipId());

		NetManager.sendUdpBroadcastMessage(message);
		delay(250);
		Serial.printf("+++++++++++++++++++++++++++++++++++++++++++++++++++++++\n");
		String updateUrl("http://");
		updateUrl += address.toString();
		updateUrl += ":8080/controller/firmware?ControllerType=";
		updateUrl += m_class;
		Serial.printf("Checking for firmware update at: %s\n", updateUrl.c_str());
		Serial.printf("+++++++++++++++++++++++++++++++++++++++++++++++++++++++\n");

		NetManager.stopUDP();
		ESPhttpUpdate.update(updateUrl, String());
		NetManager.resumeUDP();

		if (ESPhttpUpdate.getLastError() != 0)
		{
			// Print directly to the output since this is a critical error
			Serial.println("!!!!!!!!!!!!!!!!!!!!!!!!!!!!!!!!!!!!!!!!!!!!!!!!!");
			Serial.println(updateUrl.c_str());
			Serial.printf("\nFIRMWARE UPDATE FAILED:  %s\n\n", ESPhttpUpdate.getLastErrorString().c_str());
			Serial.println("!!!!!!!!!!!!!!!!!!!!!!!!!!!!!!!!!!!!!!!!!!!!!!!!!");
			restart();
		}
	}
}

void Controller::clearFiles(void)
{
	DEBUG_PRINT("CLEAR FILES!\n");
	Dir dir = SPIFFS.openDir("");
	while (dir.next())
	{
		DEBUG_PRINT("DELETING FILE %s\n", dir.fileName().c_str());
		SPIFFS.remove(dir.fileName());
	}

	Dir dir2 = SPIFFS.openDir("\\");
	while (dir2.next())
	{
		DEBUG_PRINT("DELETING FILE %s\n", dir2.fileName().c_str());
		SPIFFS.remove(dir2.fileName());
	}
}

void Controller::resetConfiguration(void)
{
	DEBUG_PRINT("Reset Configuration!\n");
	clearFiles();
}

void Controller::restart(void)
{
	UDPMessage message;
	message.setMessageID(SYS_RESTARTING);
	message.setID(ESP.getChipId());

	NetManager.sendUdpBroadcastMessage(message);
	delay(250);
	ESP.reset();
}

void Controller::networkOnline(void)
{
	DEBUG_PRINT("networkOnline\n");
	IPAddress address;
	sendControllerOnlineMessage(address);
}

void Controller::sendControllerOnlineMessage(IPAddress &address)
{
	IPAddress ip;
	ip = WiFi.localIP();
	UDPMessage message;
	message.setMessageID(SYS_CONTROLLER_ONLINE);
	message.setID(m_controllerID);
	message.setField(0, ip[0]);
	message.setField(1, ip[1]);
	message.setField(2, ip[2]);
	message.setField(3, ip[3]);
	message.setField(5, MajorVersion);
	message.setField(6, MinorVersion);
	message.setField(7, BuildVersion);

	if (address == (uint32_t)0)
		NetManager.sendUdpBroadcastMessage(message);
	else
		NetManager.sendUdpMessage(message, address, true);
}

void Controller::networkOffline(void)
{
}

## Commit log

2017-01-17 More fixes for UI sizing issues
    [main.cpp]
2017-01-21 1. Disabled new networking code. Instead, changed the UDP messaging to resend messages 3 times (for a total of 4) waiting 1 second between sends. 2. Heartbeat timers are back with a standard time out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
2017-01-22 1. New batch file to build all projects and put the compiled file in the Builds/<controller> directory 2. In all projects, replace Serial.print... with DEBUG_PRINT so release builds can be created wi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
2017-01-31 1. Refactor turnouts into TurnoutModule which handles one or more (currently two) turnouts. This enables the same module to be used in the existing TurnoutController and the future MultiController 2.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
2017-01-31 Add support for SYS_HEARTBEAT. Each controller should send it's current status in response to this message. Only controllers that actually have a status should respond. Currently, this is just the bl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
2017-03-18 1. More work on Block Controller. Still working on hardware 2. Removed redundant setup() member from module class 3. New restart() member function added to controller class which sends new SYS_RESTAR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
2017-05-26 1. ControlSever program now shuts down the Raspberry Pi when the Pi's pin 21 goes LOW. 2. -d command line argument now correctly displays debug messages when present, otherwise, no messages are displ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
    [PIGPIO.cpp, PIGPIO.h, main.cpp]
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2017-06-07 1. Remove controllerDisconnected 2. When a controller gets disconnected from the server, the TurnoutHandler sets all turnouts associated with the controller to and unknown status 3. The "Builds" sub-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
2017-06-08 1. Fix PanelController crash 2. Fix too small json buffer in Network.cpp 3. Reversed the motor pin order on SemaphoreController/SemaphoreHandler.cpp
2017-06-09 1. Command line parameters now properly processed 2. SemaphoreHandler now sending the correct json information
    [main.cpp]
2017-06-09 1. New API calls for getting a list of all controllers and sending firmware updates to controllers 2. SemaphoreHandler and controller now sends the current signal setting when the controller connects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
2017-06-09 1. Multi-controller config download now has the correct URI 2. Builds path now set correctly when downloading firmware 3. TurnoutModule.h moved pin constants to class definition 4. Call to Wire.begin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
2017-06-10 1. Add some debug statements to WebServerThread 2. Up the version number to 10 3. Double the Turnout input pin de-bounce time
2017-06-13 Cleanup of unused functions and structures for device name, controller ID and controller name.
2017-06-13 1. SemaphoreController now correctly loads current signal aspect on startup 2. Clean-up SemphoreController and TurnoutController removing old code
2017-06-22 Due to a mix-up on the panel module board, the input and output pins are reversed. Update the code to flip the input and output registers depending on the module address
2017-07-12 1. Set BlockHandler to the correct classification 2. More progress on the NCEInterface! Still need to fix threading issues
2017-07-12 Fix threading issues with NCEInterface and add a small state machine to track the current connection status
2017-10-05 1. Add PanelRoute table to database which tracks what routes and panel's output LED is assigned to 2. More work on converting UDPTester to use json/ControlServer
2017-10-06 Fixing issues with incorrect data being sent to a controller when a device is attached to more than one panel (an aux panel)
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2017-10-17 1. Re-factor sending messages so that ACKs/errors raise a signal allowing interested parties to act accordingly 2. TurnoutHandler now waits until message is ACKed before updating the turnout state 3.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
    [main.cpp]
2017-10-19 1. Fix to make sure BlockHandler identifies the current state of a block properly 2. Add DISTINCT to select to make sure only one signalID is returned (no duplicates)
2017-10-28 1. Add eagle printed circuit board files 2. Additions to API 3. Remove a bunch of "unused variable" warnings 4. SignalHandler/SemaphoreHandler now processes the aspect conditions in the proper order 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
    [BlockController.brd, BlockController.sch, ESP8266Controller.brd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]
2017-10-29 1. More additions to the API 2. Rename device.moduleIndex to device.port 3. Begin work on new InputModule 4. Module: remove unused functions: virtual byte getDeviceCount(void) const = 0; virtual shor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
    [ESP8266Controller.brd, ESP8266Controller.sch]
2017-10-30 Database cleanup complete:
    1. Remove signal and block tables
    2. change device.moduleIndex to port
    3. Change controllerModule.moduleIndex to address
    4. change routeEntry.turnoutID to deviceID
    5. change signalAspectCondition to signalAspect
    6. change signalAspect.signalID to deviceID
    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
2017-11-06 1. Cleanup continues. BlockController and the corresponding controller are deprecated along with SignalController and it's controller board. These are replaced by the InputModule and OutputModule res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
    [BlockController.brd, BlockController.sch, ESP8266Controller.brd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]
2017-11-13 1. Fixes for new Input/Output module and the server side handlers that need to use them 2. Add a timeout to NetworkClass to restart the controller if the device is disconnected from the server for mo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
2017-12-06 ****** VERSION 3 *****************
    1. A return to the original design with a twist. Instead of relying on UDP broadcast messages, each controller now maintains a list of controllers it needs to notify whenever a state change happens i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
    2. The role of the ControlServer (soon to be renamed LCSServer) has changed to be the primary interface device and the API server. It's role as manager/keeper of the database has not changed.
    3. Cont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
2017-12-06 ControlServer is now LCSServer completing the re-naming of the Arduino project to Layout Control System (LCS)
2017-12-06 1. Updates/fixes for LCSServer name change 2. Add ability to print labels for controllers and modules (Only tested with Dymo LabelWriter 450)
    [main.cpp]
2017-12-10 1. Database updated with new schema and data converted to match. Renamed lcs.db database added 2. sendControllerNotificationList added to API 3. Adding and deleting controllers now working properly 4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
    [Controller.cpp]
2017-12-11 1. Latest version of the database checked in 2. Updates to the device list in the ManageDevices2.qml 3. Download issue fixed for handleGetDeviceList (more work needs to be done here)
2017-12-13 1. Add message ACKS to retry messages 2. Fix incorrect loading of module config data
    [Controller.cpp, LCSController.ino]
2017-12-14 1. Cleanup work 2. Reduced the retry timeout to 2 seconds (from 3) 3. Change the TurnoutModule board to use the same address pins as the other modules 4. Add a two-pin header to Input and Output modu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
    [InputModule.brd, InputModule.sch, OutputModule.brd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]
2017-12-15 1. Fixes for SemaphoreDevice and SignalDevice 2. Start fixes on BlockDevice. Still not finished
    [SemaphoreDevice.cpp]
2017-12-18 1. Fixes for Block Device 2. Move NetworkManager.init() call earlier in the controller setup() function 3. Application Server now properly ACK's UDP messages
    [Controller.cpp, LCSController.ino]
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2017-12-20 1. Split Signal Device configuration into multiple downloads. More work needed on this...
2017-12-20 Refactoring of Device Configuration complete. Now, the device configuration file contains two lists; a list of aspects for this signal and a list of devices to monitor. Each aspect is then downloaded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
2017-12-21 Fixes for signal device. Still more work to be done
    [Controller.cpp]
2017-12-21 1. Documentation updates 2. Fix saving Signal aspects 3. Fix NetworkManager's handling of SYS_CONTROLLER_ONLINE. Send status message if the controller is found in the list even if the address passed 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
    [Controller.cpp, TurnoutDevice.cpp]
2017-12-24 1. Add jitter-detection to BlockDevice 2. Add flashing pins to ModuleData 3. Move flashing pin code from PanelOutputDevice to OutputModule. This insures pins blink at the same rate and same state. 4.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
    [ESP8266Controller.brd, ESP8266Controller.sch]
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2017-12-26 1. Add new overhead controller to database and new module and devices 2. Fix more duplicate records this time in output devices
2017-12-28 1. Start process of re-factoring API 2. Start process of re-factoring the LCSAdmin UI 3. Add ability to create a copy of a device to the API
2018-01-13 1. Add copyDevice to API 2. Add modelChanged property to JSonModel
    [ESP8266Controller.brd, ESP8266Controller.sch, InputModule.brd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]
2018-01-13 Re-re commit of change that has the network module initialize after all modules and devices are created and initialized. This ensures that network messages do not arrive before all modules and device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
2018-01-22 Re-factoring of API complete. APIHandler replaced by APIController, APISignal, APIDevice, APITurnout, APIEntity, APIRoute API Documentation also updated.
    [main.cpp]
2018-01-29 1. Split device into two tables: device and moduleDevicePort. This allows a device to be assigned to multiple modules...useful for PanelInputDevice, PanelOutputDevice and SignalDevice's. 2. Removed c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
    [main.cpp]
2018-01-31 1. New labelName field in device table which is used for the printed label for cases where the deviceName is too large to fit on a label. 2. Update API module_device_port function to return the devic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
2018-02-06 Changes for create_device api function. Now this function takes a JSON body filled with the new device name, description and device class. If the createExtra flag is set to true, additional devices a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
2018-03-01 1. Change order by clause for getControllerModuleList to order by moduleName of a controllerID is not supplied. 2. Restore de-bounce code in BlockDevice.
2018-03-13 1. Updates to database. Rename Signal entries to S[block name]. Rename blocks to B[block name] 2. Add friendly device state text to DeviceList.qml 3. Change release mode debug baud rate to 115200 to 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
    [LCSController.ino]
2018-03-24 1. Database updates which includes all devices, modules and controllers to complete CA 2. Fix device list showing updated data after editing 3. JsonModel::setEntity now correctly marks the entity's r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
2018-03-25 1. New module device list page 2. New module drop-down box when adding a module to a device
2018-03-25 1. Fix issue with sending large data results back 2. Add missing devices for CA
2018-03-30 Fix deleting a device
2018-04-02 1. More adjustments to block detector 2. Expander8 and Expander16 classes now impose a retry count. More than three failed read/write attempts causes the module to be disabled. 3. Signals now allow f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
    [TurnoutModule.brd, TurnoutModule.sch]
2018-04-04 1. Change the way messages are generated. Now, an out message is created per module so that a group of up to 8 devices can be combined into a single DEVICE_STATUS message. 2. NetworkManager now check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
    [Controller.cpp, LCSController.ino]
2018-04-05 Fix issues with device manager handing new DEVICE_STATUS message
2018-04-05 1. Add getDeviceType() to all devices. 2. Fix bugs in DEVICE_STATUS messages
    [Controller.cpp, LCSController.ino]
2018-04-06 1. Change getSignalConfig to only return the aspect ID's and the list of devices. 2. Fix issue with SignalDevice not properly handling OR conditions
2018-04-08 1. Fix warning about waitForDisconnected when socket is already closed 2. Fix issue with disable checkbox now working on Controller Module list
2018-04-09 1. Fix InputModule's handling of the DEVICE_STATUS message 2. Fix issue with NetworkManager not properly sending status messages when a new controller goes online. 3. Increase the number of devices a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
2018-04-10 1. Fix wrong size of UDPMessageStruct 2. Add idle timeout to NetworkManager which sends a SYS_ACK heartbeat message every 2 minutes of idle time 3. Update build number to 3.0.28
    [LCSController.ino]
2018-04-11 1. Remove debug statements from NetworkManager 2. Fix strange issue with SemaphoreDevice...works for now but more investigation is needed
    [SemaphoreDevice.cpp]
2018-04-11 1. Add labelName to GenericDeviceDetails and to the API 2. Change printing labels for modules to print the name of the module instead of the module type.
2018-04-16 1. Add server drop down for admin application 2. Add busy indicator 3. Fix issue with adding route entries not working properly 4. Add route list to turnout details.
    [main.cpp]
2018-04-20 1. Add option to SignalDevice to change the pin ON value to either 0 or 1 depending on what the signal LED requires 2. Fix save issues with Routes and Devices
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2018-04-27 1. Data entry for overhead panel for all blocks in CA 2. Temporarily rollback changes to SignalDevice 3. Fix issue with ModuleDevices.qml not properly setting the deviceID
2018-05-12 1. New DeviceMonitor class tracks current device status for all modules 2. Update process of storing and loading configuration data for Input, Output and Turnout devices to store the data in binary f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
2018-05-13 1. Fix issue with saved turnout configuration data 2. PanelOutputDevice now correctly adds the device ID to the DeviceMonitor 3. Change version to 3.0.32
    [TurnoutDevice.cpp]
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2019-01-16 Add missing RouteMonitor files
    [RouteMonitor.cpp]
2019-01-20 1. Increase MAX_ROUTE_ENTRIES to 10 2. Add some debugging statements to TurnoutDevice 3. Fix issue with PanelOutputDevice to always update DeviceMonitor when a new UDP message arrives
    [TurnoutDevice.cpp]
2019-01-27 New Update!
    1. Documentation checked in
    2. Two new messages: SYS_DEVICE_CONFIG_CHANGED and SYS_ROUTE_CONFIG_CHANGED are now sent out by the API whenever a route or a device's configuration is changed. The controllers respond by downloading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
    3. TurnoutDetails.qml now has the DeviceProperties section displayed
    4. PanelOutputDevice now supports multiple routes. When ONVALUE is set to 1, the LED remains ON if ANY of the routes are active. When ONVALUE is set to 0, the LED is ON only if ALL routes are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
    [ESP8266Controller.brd, ESP8266Controller.sch, PartsList.xlsx]
2019-01-27 1. Minor bug fixes 2. Add LCSOverview.pdf 3. DeviceProperties.qml component now uses a combo box for ITEMID and ROUTEID entries 4. New toolbar "Send Firmware" button on the Controllers tab sends firm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
    [RouteMonitor.cpp]
2019-01-29 1. Possible fixes to the firmware update procedure. For some reason, the firmware update process works on some networks but not the club's.
    [Controller.cpp]
2019-02-03 1. Fix some serial prints so that certain critical errors get sent to the serial output even if DEBUG_PRINT is commented out 2. Add a DEBUG_PRINT line to DeviceMonitor.addDevice() 3. Make sure the Ro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
    [Controller.cpp, LCSController.ino, RouteMonitor.cpp]
2019-02-10 1. DeviceMonitor now automatically adds a device if the getStatus is called on a device that is not currently being tracked. 2. Modify PanelOutputDataStruct to include a list of routes instead of dyn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
    [RouteMonitor.cpp]

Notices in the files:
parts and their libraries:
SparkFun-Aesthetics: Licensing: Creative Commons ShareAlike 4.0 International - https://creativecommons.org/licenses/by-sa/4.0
